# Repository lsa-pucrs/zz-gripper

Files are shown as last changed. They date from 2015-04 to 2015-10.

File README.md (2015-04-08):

# ZZ-Gripper v1.0

####Introdução: ####
Feita no laboratório de sistemas autônomos, [LSA](https://www.inf.pucrs.br/felipe.meneguzzi/lsa/), da FACIN na PUCRS.
Esta gripper foi desenvolvida no laboratório visando aplicações _pick-and-place_ em conjunto com o robo Turtlebot.

<p align="center">
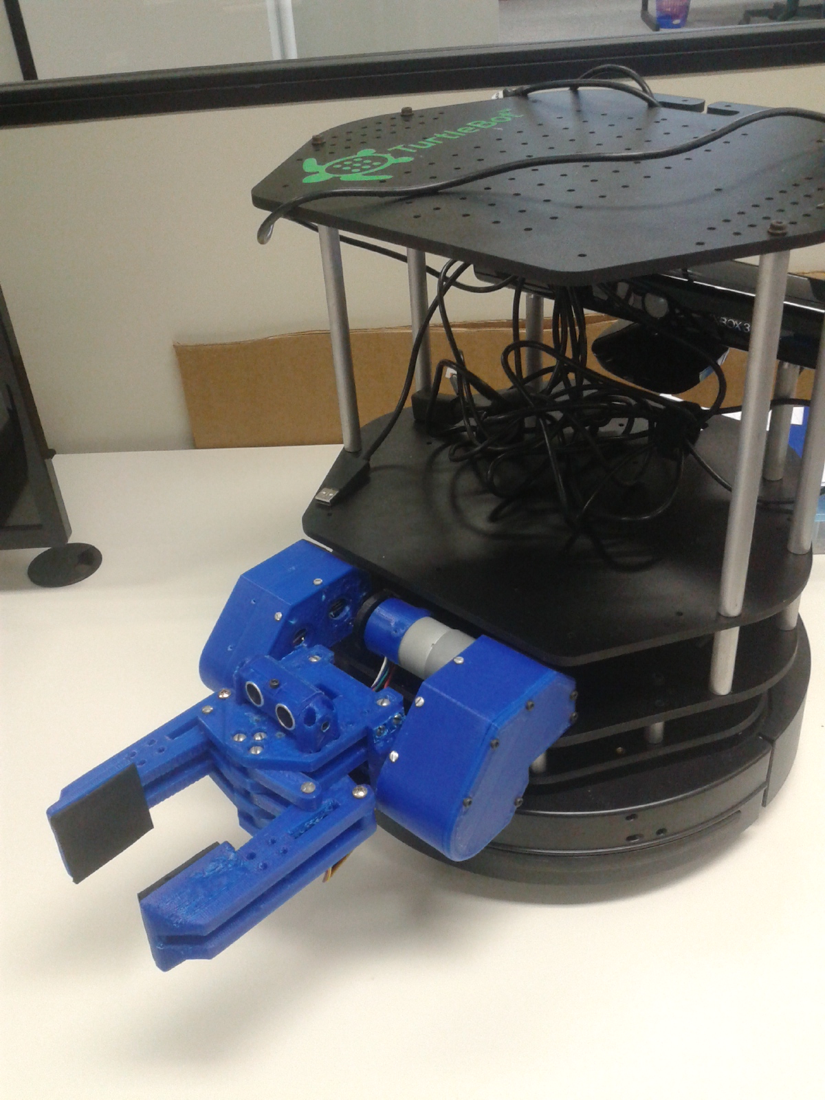
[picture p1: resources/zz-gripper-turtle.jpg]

</P>

####Especificações:####
+ Microcontrolador: Arduino nano
+ Driver: TB6612-Dual Motor Driver
+ Atuadores: 2 Graus de liberdade
+ Sensores: Sensor de força, sensor ultrasonico, sensor de corrente, chave fim de curso.
+ Peso (partes plasticas): ?
+ Peso total: ?
+ Custo total: ?
+ Tempo para construção: ?
+ Dimenções: ?
+ Força aplicada a objeto: ~500g
+ Peso máximo de sustentação: ~700g

####TO-DO_List:####
- [ ] Manual ZZ-Gripper v1.0
- [ ] Teste funcional por ssh (sem alimentação externa)
- [x] Projeto Solidworks
- [x] Driver exemplo ROS
- [x] Esquema elétrico da placa de controle

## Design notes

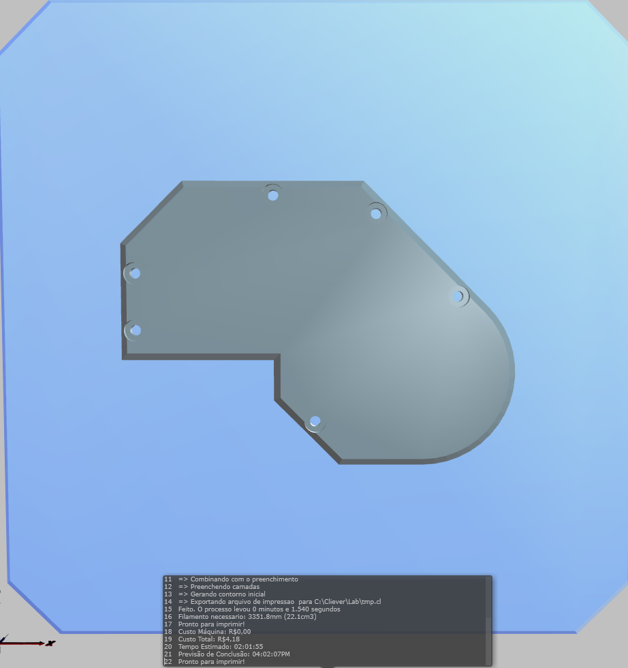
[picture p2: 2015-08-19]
stl_files/zz_gripper-specifications/gripper_support/motorPlate-board_lid.png

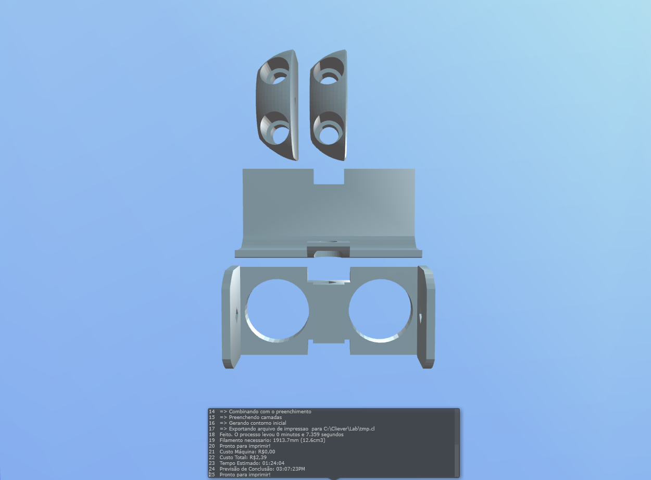
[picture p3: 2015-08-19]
stl_files/zz_gripper-specifications/sonar_support/sonar_support.png

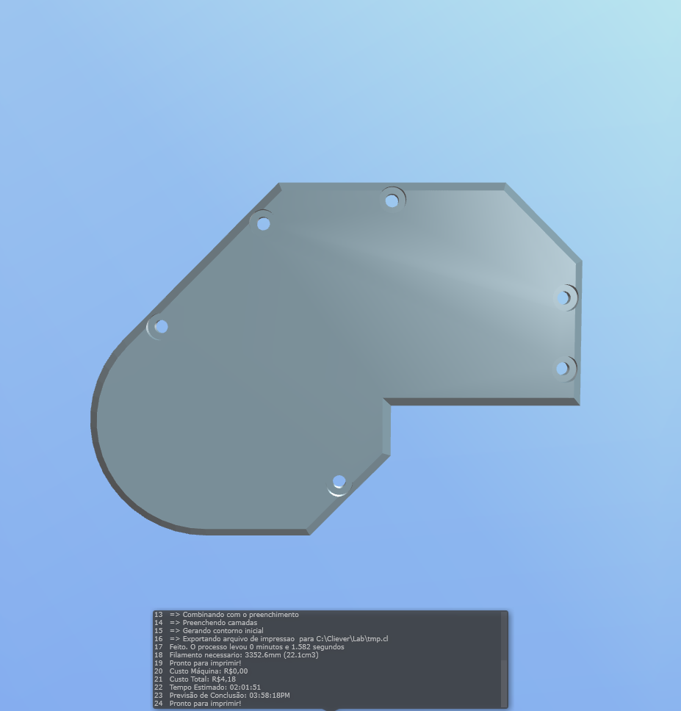
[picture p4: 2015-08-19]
stl_files/zz_gripper-specifications/gripper_support/motorPlate-lid.png

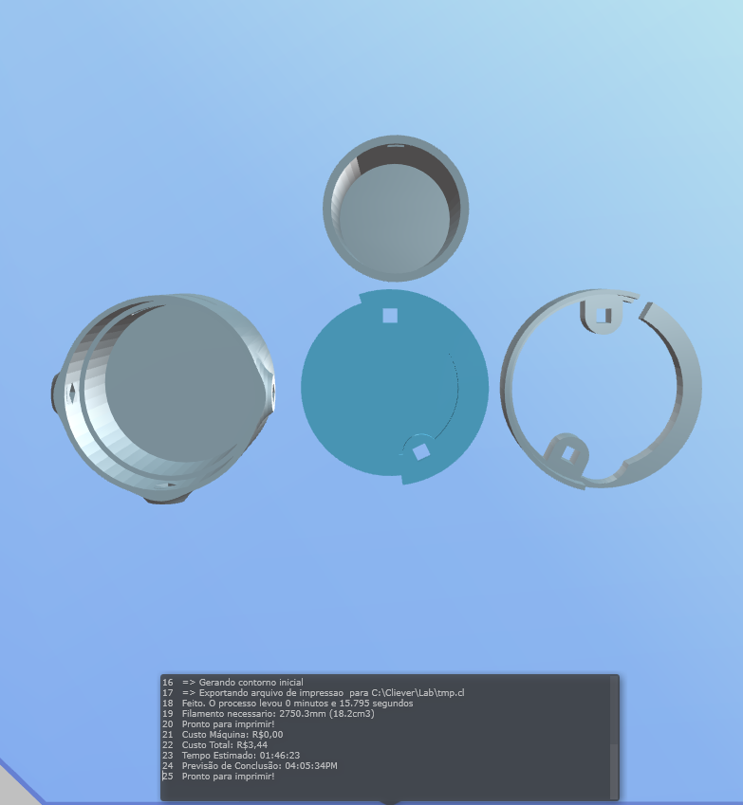
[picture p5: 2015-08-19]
stl_files/zz_gripper-specifications/gripper_support/motor_Case-and-board_protection.png

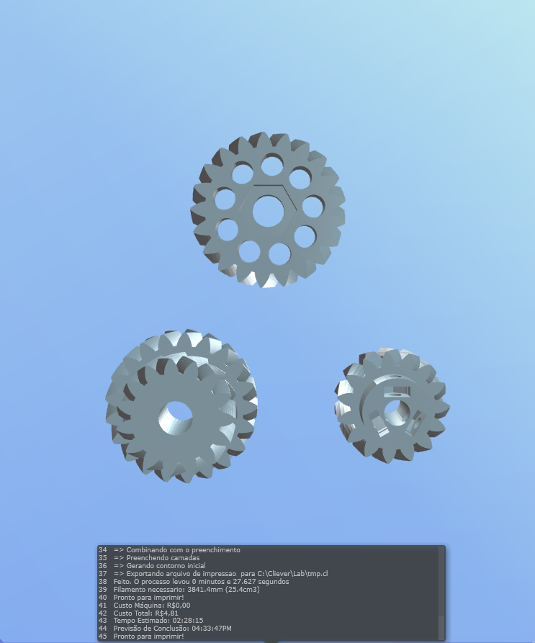
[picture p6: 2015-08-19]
stl_files/zz_gripper-specifications/gripper_support/gears/gears.png

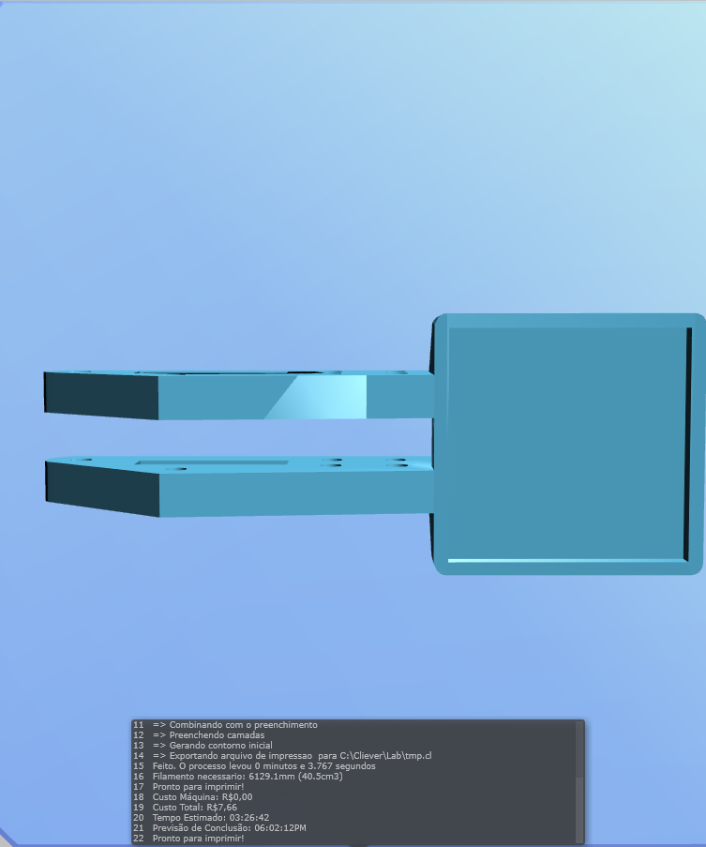
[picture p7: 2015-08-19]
stl_files/zz_gripper-specifications/gripper_hand/gripper_finger--DroidGripper-RightArm.png

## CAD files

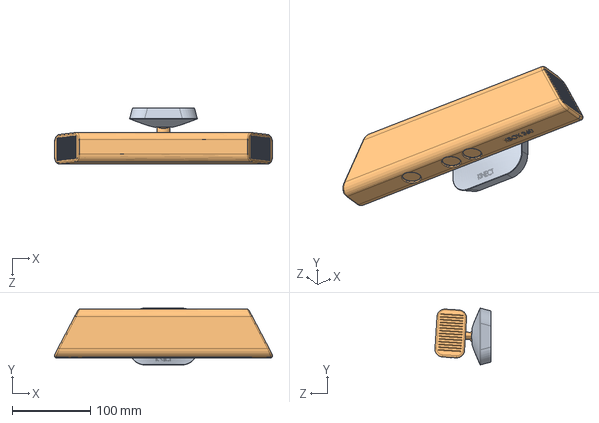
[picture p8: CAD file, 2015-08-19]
solidworks/turtlebot_2-converted_model/others/kinect/1_kinect_assembly.SLDASM
279.4 x 72.8 x 71.8 mm
base KINECT
KINECT XBOX

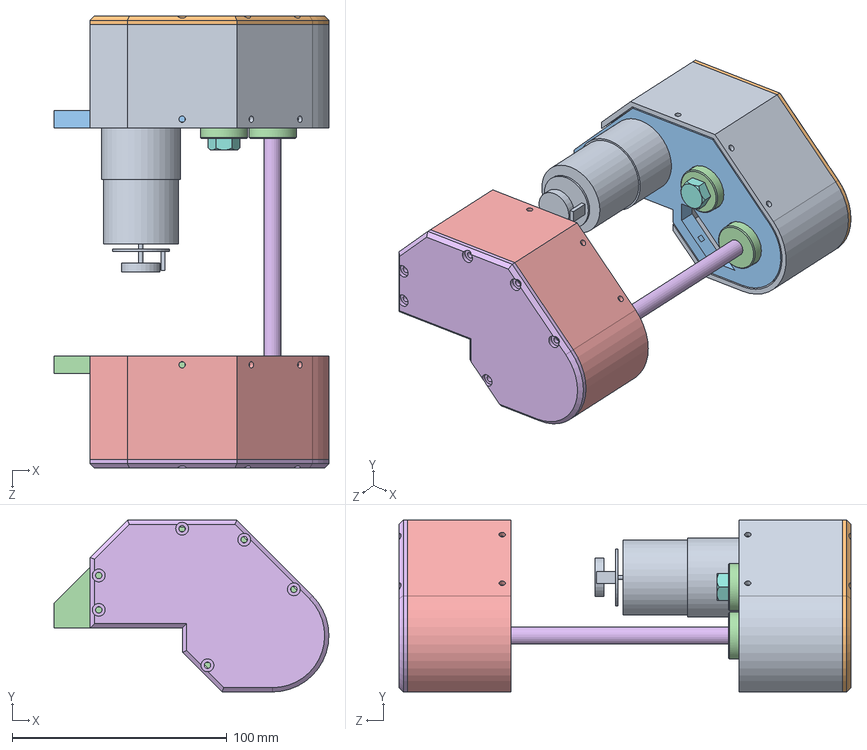
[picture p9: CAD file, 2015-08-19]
solidworks/zz_gripper-model/1_gripper_assembly.SLDASM
127.9 x 79.9 x 210.3 mm
motorPlate-case
motorPlate-lid
motorPlate
bearing x 4
nut x 3
threaded_rod
rod_gear_big_simple
bolt
motor_pololu
motor_gear_simple
reduction_gear_simple
motorPlate-board
motorPlate-board_case
motorPlate-board_lid

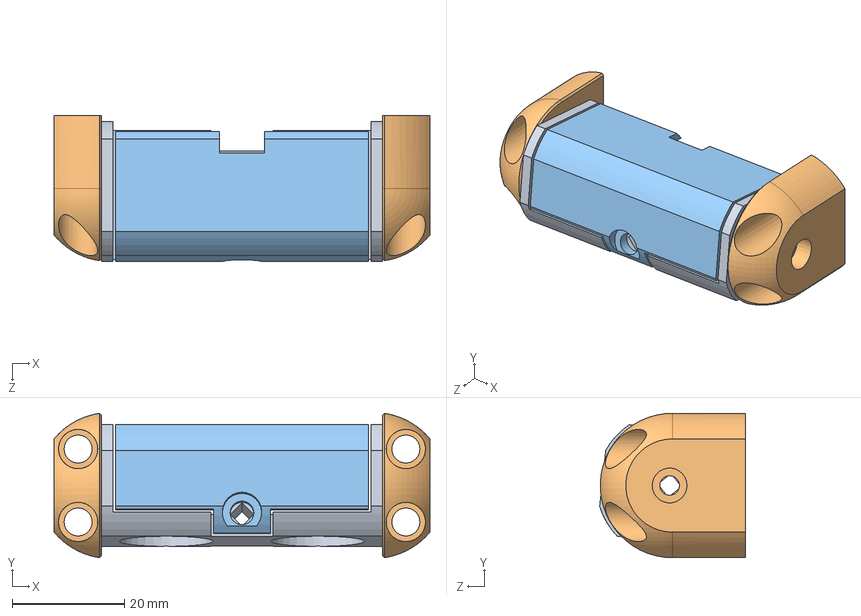
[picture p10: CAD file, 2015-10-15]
solidworks/zz_gripper-model/sonar_support/1_sonar_support_assembly.SLDASM
67.0 x 25.7 x 26.0 mm
sonar-case
sonar-support x 2
sonar-lid

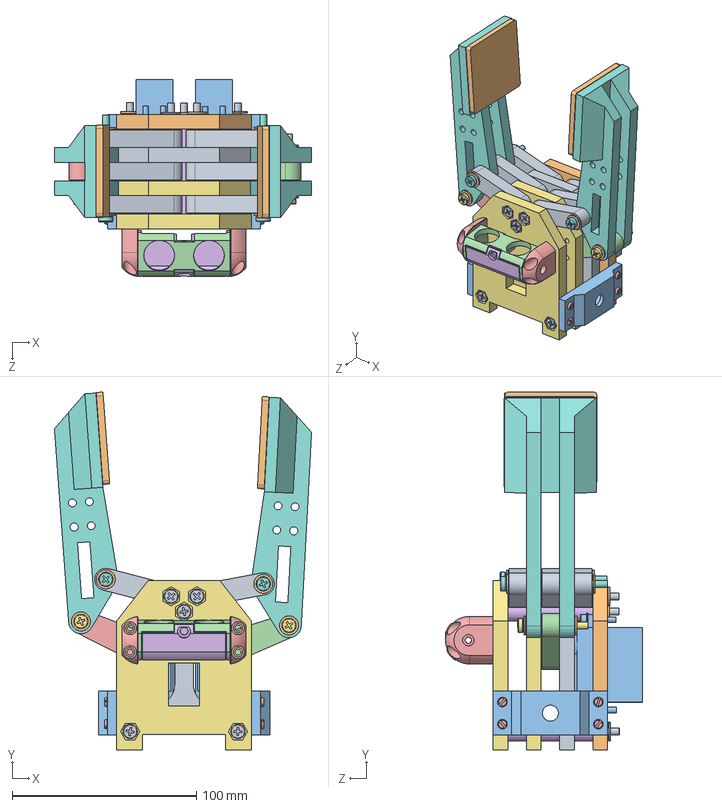
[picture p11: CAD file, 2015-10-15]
solidworks/zz_gripper-model/gripper_hand/1_hand_assembly.SLDASM
139.4 x 194.1 x 107.0 mm
gripperGearPlate
gripperServoPlate
MG996R_Another x 2
leftDriveGear
rightDriveGear
plate_spacer x 9
gripperSuportPlate x 2
gripper_finger x 2
gripper_interface_link x 6
pressurePlate x 2
main_axis_nut_reinforcement x 2
sonar-case
sonar-support x 2
sonar-lid
PPh-M4x35mm x 2
PPh-M4x55mm x 2
PPh-M4x65mm x 5
washer-M4 x 13
PA-M3x16mm x 8
washer-M3 x 8
FCA-2_85Dx13mm x 8

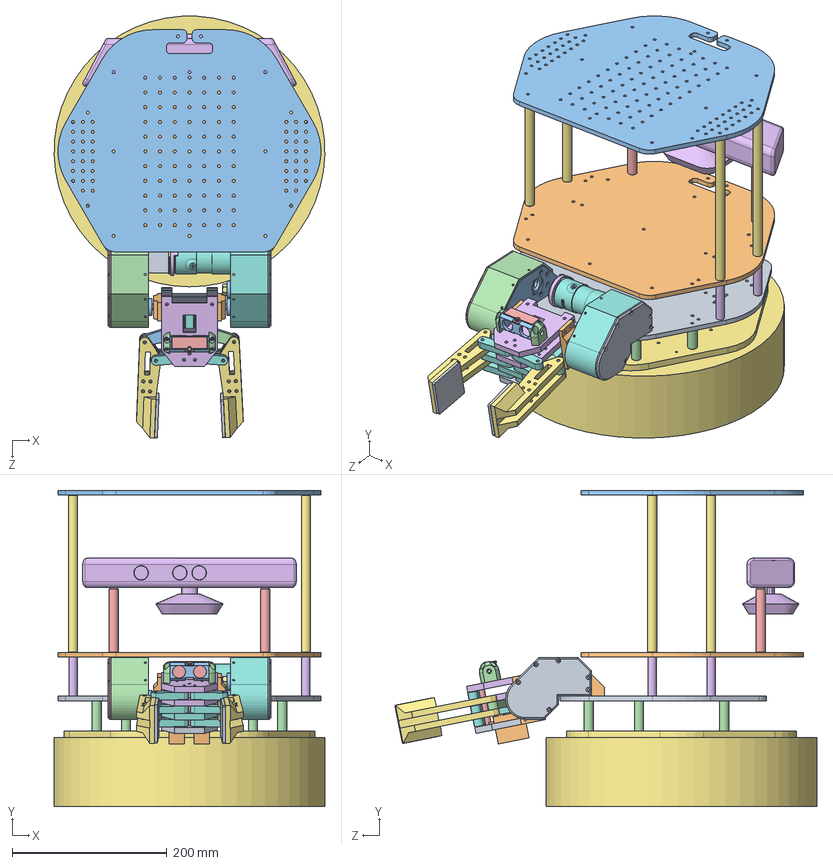
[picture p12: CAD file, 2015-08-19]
solidworks/turtlebot_2-converted_model/1_turtlebot_assembly.SLDASM
349.8 x 408.7 x 545.4 mm
plate_bottom
plate_middle_
plate_top_
pole_bottom_ x 6
pole_kinect_ x 2
pole_middle_ x 4
pole_top_ x 4
motorPlate-case
motorPlate-lid
motorPlate
bearing x 6
nut x 3
threaded_rod
rod_gear_big_simple
bolt
motor_pololu
motor_gear_simple
reduction_gear_simple
motorPlate-board
motorPlate-board_case
motorPlate-board_lid
Kinect_Sensor_68-04546
base
gripperGearPlate
gripperServoPlate
MG996R_Another x 2
leftDriveGear
rightDriveGear
plate_spacer x 9
gripperSuportPlate x 2
gripper_finger x 2
gripper_interface_link x 6
pressurePlate x 2
main_axis_nut_reinforcement x 2
sonar-case
sonar-support x 2
sonar-lid
motor_case-endstop_support
motor_case-endstop_support-lid
motor_case

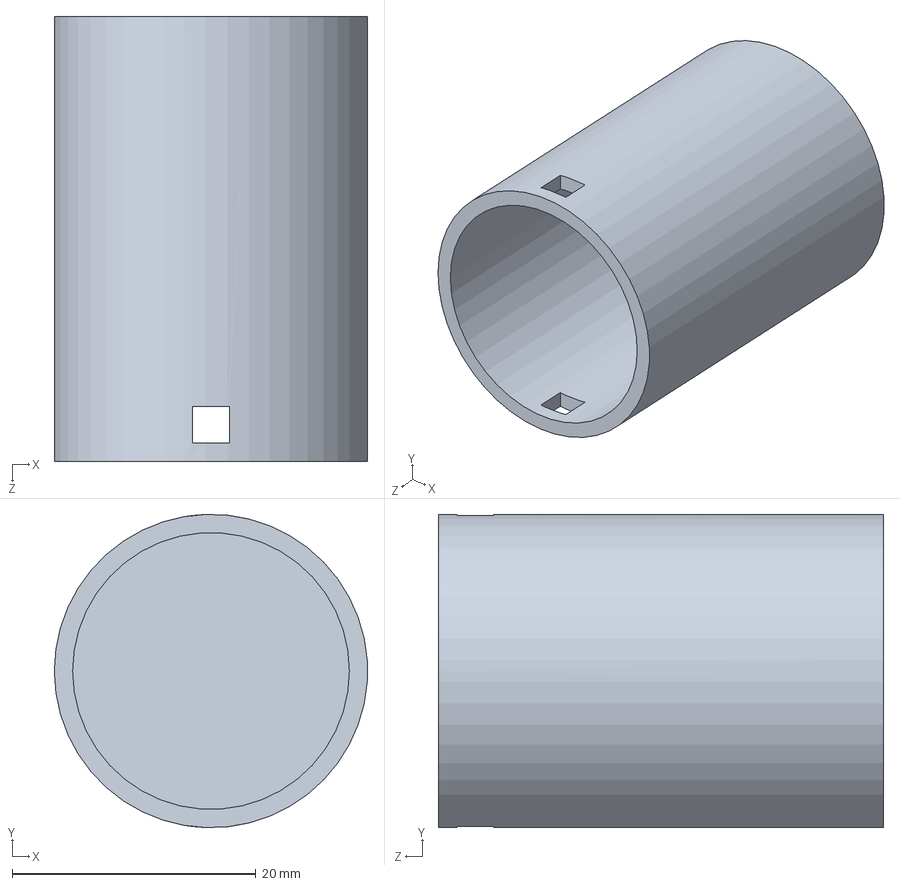
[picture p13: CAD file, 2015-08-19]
solidworks/zz_gripper-model/gripper_support/main_axys-board_protection.SLDPRT
25.7 x 25.7 x 36.5 mm

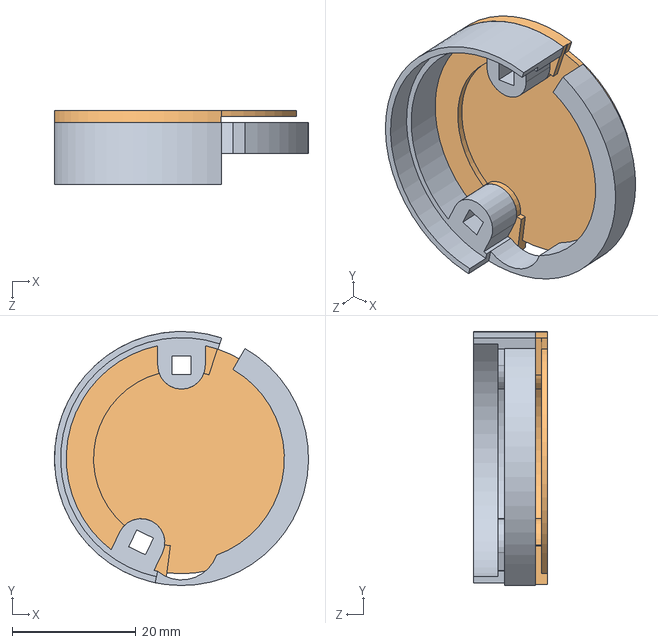
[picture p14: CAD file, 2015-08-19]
solidworks/zz_gripper-model/gripper_support/2_support_endstop.SLDASM
41.0 x 41.0 x 12.0 mm
motor_case-endstop_support
motor_case-endstop_support-lid

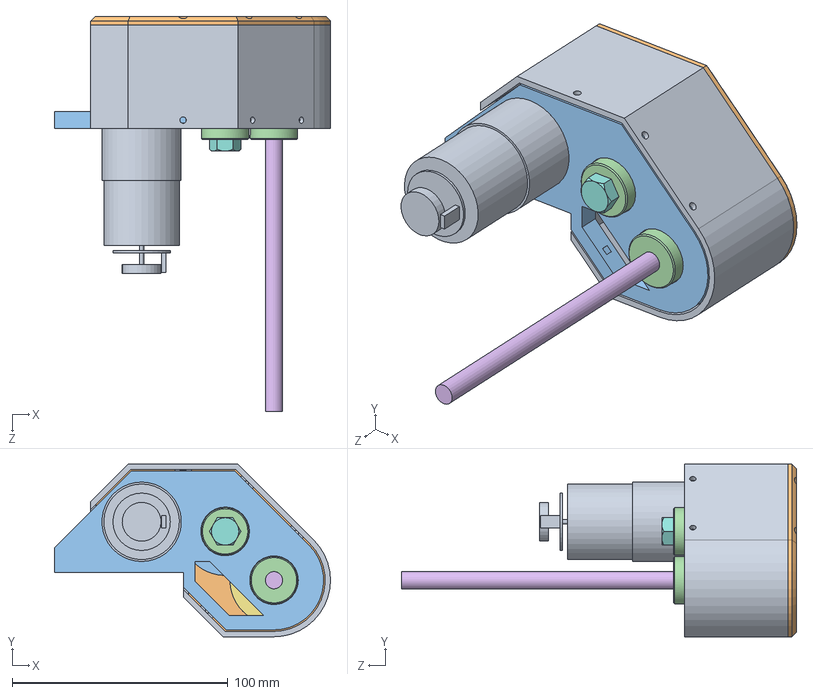
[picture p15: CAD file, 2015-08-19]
solidworks/zz_gripper-model/gripper_support/1_support_assembly.SLDASM
127.9 x 79.9 x 183.0 mm
motorPlate-case
motorPlate-lid
motorPlate
bearing x 4
nut x 3
threaded_rod
rod_gear_big_simple
bolt
motor_pololu
motor_gear_simple
reduction_gear_simple

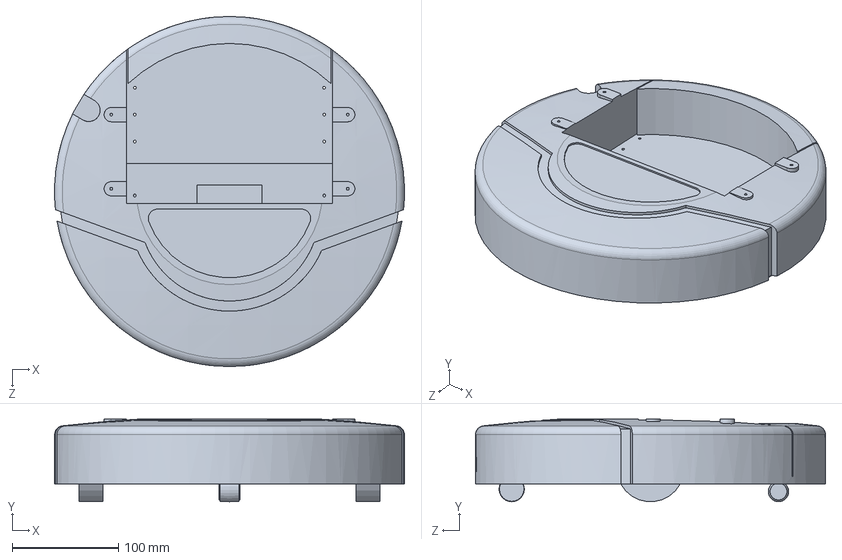
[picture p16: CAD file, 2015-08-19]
solidworks/turtlebot_2-converted_model/others/iRobot_Create_68-04545.SLDPRT
329.9 x 77.8 x 330.0 mm

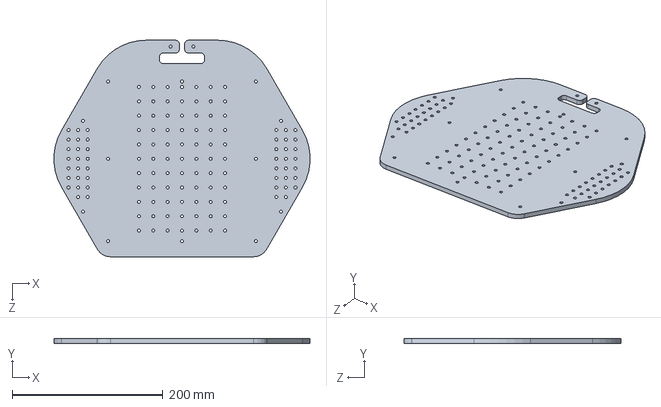
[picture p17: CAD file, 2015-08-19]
solidworks/turtlebot_2-converted_model/plate_top_.SLDPRT
339.6 x 6.00 x 287.3 mm

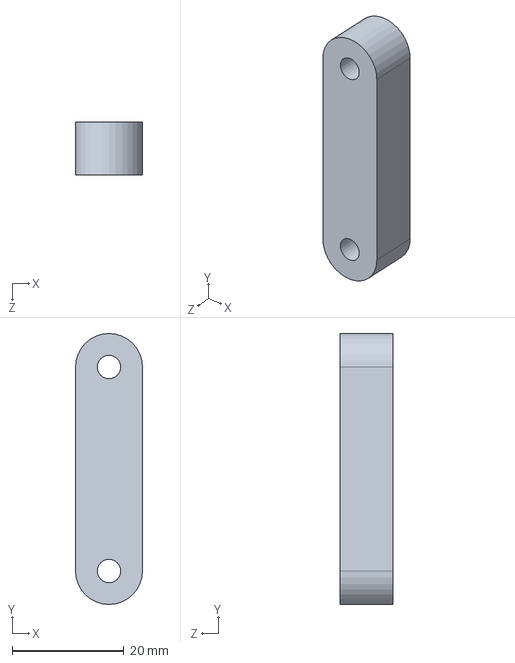
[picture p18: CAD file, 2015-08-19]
solidworks/zz_gripper-model/gripper_hand/converted/gripper_interface_link.SLDPRT
12.0 x 48.6 x 9.50 mm

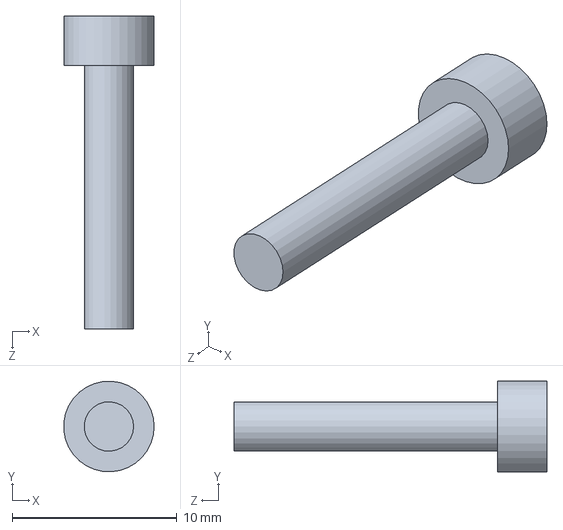
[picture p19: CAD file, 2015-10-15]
solidworks/zz_gripper-model/gripper_hand/resources/PA-M3x16mm.SLDPRT
5.49 x 5.49 x 19.0 mm

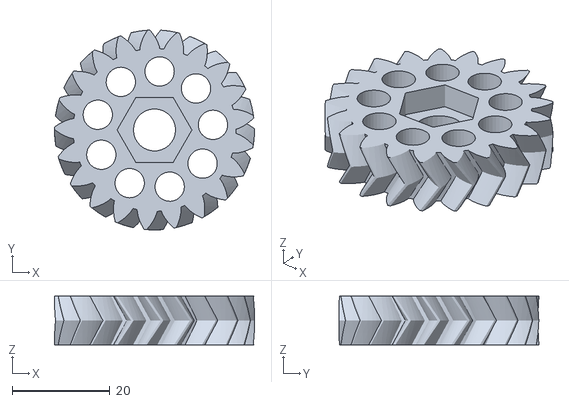
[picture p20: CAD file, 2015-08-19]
solidworks/zz_gripper-model/gripper_support/gears/rod_gear_big.stl
40.9 x 40.9 x 10.0

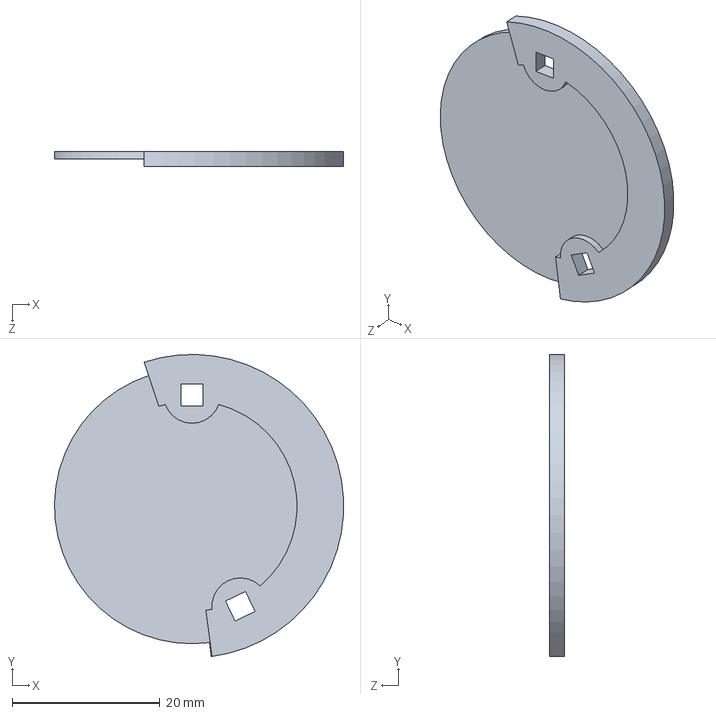
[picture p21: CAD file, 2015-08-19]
solidworks/zz_gripper-model/gripper_support/motor_case-endstop_support-lid.SLDPRT
39.1 x 40.8 x 2.00 mm

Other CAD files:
solidworks/zz_gripper-model/gripper_support/others/motor_pololu.SLDPRT
stl_files/zz_gripper-parts/gripper_hand/6x-gripper_interface_link--DroidGripper-InterfaceLinks.stl
stl_files/zz_gripper-parts/gripper_hand/new_parts/6x-plate_spacer.STL
stl_files/zz_gripper-parts/sonar_support/2x-sonar-support.STL
solidworks/zz_gripper-model/gripper_support/gears/motor_gear.scad
solidworks/zz_gripper-model/gripper_support/gears/reduction_gear.scad
solidworks/zz_gripper-model/gripper_support/gears/rod_gear_big.scad
solidworks/zz_gripper-model/gripper_support/gears/resource/rod_gear.scad
solidworks/turtlebot_2-converted_model/base.SLDPRT
solidworks/turtlebot_2-converted_model/counterweight_.SLDPRT
solidworks/turtlebot_2-converted_model/others/Kinect_Sensor_68-04546.SLDPRT
solidworks/turtlebot_2-converted_model/others/kinect/KINECT XBOX.SLDPRT
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

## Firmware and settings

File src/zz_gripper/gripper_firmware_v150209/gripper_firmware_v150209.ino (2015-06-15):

/*
Force Sensor A201-25 (0-25 lb. force range 111.205N) acessado em http://www.phidgets.com/documentation/Phidgets/3100_0_FlexiforceUserManual.pdf
Rotation Speed ~38.27rpm source: Motor Pololu 70:1 = 150RPM em 12v =  (((15.0/21)**2)*150)/2^= ~38.27

Servo mg996:
Velocidade de operação: 0.13sec / 60 graus (6.0V sem carga) = 0.174seg 80graus
Torque Stall: 15 kg-cm (208,3 oz-in) em 6V
*/
#include "gripper_firmware.h"
#include <PWMServo.h> //tem que estar no .h e no sketch
#include <ros.h>
#include <std_msgs/String.h>
#include <std_msgs/UInt8.h>
#include <std_msgs/UInt16.h>
#include <std_msgs/Int16.h>



ros::NodeHandle nh;

void callCommand( const std_msgs::String& gripper_msg){
  readString=gripper_msg.data;
}

std_msgs::String status_msg;
std_msgs::UInt16 topicSpeed;
std_msgs::Int16 topicPosition;
std_msgs::UInt8 topicDistance;
std_msgs::UInt16 topicForce;
std_msgs::Int16 topicRotationX;

ros::Subscriber<std_msgs::String> subGripperCommands("gripperCommands" , callCommand);

ros::Publisher advGripperSpeed("gripperSpeed", &topicSpeed);
ros::Publisher advGripperForce("gripperForce", &topicForce);
ros::Publisher advGripperPosition("gripperPosition", &topicPosition);
ros::Publisher advGripperDistance("gripperDistance", &topicDistance);
ros::Publisher advGripperRotationX("gripperRotationX", &topicRotationX);

void setup()   {
  pinMode(dirPin,OUTPUT);
  pinMode(pwmPin,OUTPUT);
  pinMode(inputBPin,INPUT); //inputB // white wire
  pinMode(homePin,INPUT);
  attachInterrupt(inputAPin,incA,FALLING); //pin 2 inputA // yellow wire

  //gripper
  gpp_R.attach(servoRPin);  
  gpp_L.attach(servoLPin);
  //#gripper
  nh.initNode();
  nh.subscribe(subGripperCommands);
  nh.advertise(advGripperSpeed);
  nh.advertise(advGripperForce);
  nh.advertise(advGripperPosition);
  nh.advertise(advGripperDistance);
  nh.advertise(advGripperRotationX);

  nh.spinOnce();
  delay(50);
}



void loop(){
  //ROS PUBLISHERS
  topicForce.data = gripperForce;
  advGripperForce.publish(&topicForce);
  topicPosition.data = gripperPosition;
  advGripperPosition.publish(&topicPosition);
  topicRotationX.data = gripperRotationX;
  advGripperRotationX.publish(&topicRotationX);
  topicDistance.data = gripperDistance;
  advGripperDistance.publish(&topicDistance);

  //encoder dalay
  time = millis();
  unsigned long rotationDelay = time - lastTimeRotationDelay;
  if(rotationDelay >= gripperSpeedSetPoint/10){ // dividido por 10 pois, 5ms é o delay ideal dealy deafault: 50ms
    lastTimeRotationDelay = time;
    if(ComposedSetPoint<gripperRotationXSetPoint)ComposedSetPoint++;
    if(ComposedSetPoint>gripperRotationXSetPoint)ComposedSetPoint--;
    computeEncoderX(ComposedSetPoint);
  }


  //compute command delay
  time = millis();
  unsigned long wait = time - lastTime;  
  if(wait >= 100){ //amory: declarar como constante
    lastTime = time;
    computeCommand(readString);
    //gripperForce = analogRead(forceSensorPin);//map(gripperForce,0,111,1023,0); //4.2v = 111N = 11.34kg
    //gripperDistance = measureDistance();
    //gripperCurrent = analogRead(currentSensorPin);
  }

  updateGripperActions();

  unsigned long waitSpinOnce = time - lastTimeSpinOnce;  
  if(waitSpinOnce >= 50){ 
    lastTimeSpinOnce = time;
    nh.spinOnce(); //evitar delay pois afeta na movimentacao da gripper
  }
}

void incA(){
  inputB = digitalRead(inputBPin);
  if(inputB)gripperRotationX--;
  else gripperRotationX++;
}

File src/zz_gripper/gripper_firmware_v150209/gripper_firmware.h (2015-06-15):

#include "Arduino.h" //needed for Serial.println
#include <PWMServo.h> 

//digital pins
#define servoRPin 10
#define servoLPin 9
#define trigPin 8 
#define echoPin 7 
#define pwmPin 6
#define dirPin 5
#define inputBPin 4
#define homePin 3
#define inputAPin 0 //interrupt 0 -> pin 2

//analogic pins
#define forceSensorPin 0
#define BAUDRATE 9600


//commandVariables
String readString; //para entrada serial
String commandName="";
int16_t commandValue=0;
boolean commandDone = false;

//gripperVariables
boolean gripperActive = true;
uint16_t gripperSpeedSetPoint = 50;
int16_t gripperPosition;
int16_t gripperPositionSetPoint;
int8_t gripperMode = 0; //0 open/ 1 close/ 2 auto
int8_t lastGripperMode = 1;
PWMServo gpp_R;  
PWMServo gpp_L; 
boolean gripperState = false;
//Right 45 min, 60 mid, 150 max 
int16_t gpp_RMax = 136;///160;
int16_t gpp_RMin = 55;
//Left 145 min, 120 mid, 50 max
int16_t gpp_LMax = 34; //30
int16_t gpp_LMin = 120;
//////////////////////////
int16_t gpp_RPos = gpp_RMin;
int16_t gpp_LPos = gpp_LMin;

//sonar
uint8_t gripperDistance;
uint8_t gripperDistanceSetPoint = 15;
boolean sonarActive = false;
boolean sonarFlag = false; //when it found something

//forceSensor
uint16_t gripperForce;
uint16_t gripperForceSetPoint = 50; //hard 0; easy 1024; to activate

//encoder
int16_t ITerm1 = 0, ITerm2 = 0;
int16_t ComposedSetPoint;
int16_t gripperRotationXSetPoint;
volatile int16_t gripperRotationX = 0;
volatile boolean inputB = false;
double n = 0;
double pwmValue = 0;

//general
int val;
unsigned long time;
unsigned long lastTime;
unsigned long lastTimeCloseDelay;
unsigned long lastTimeRotationDelay;
unsigned long lastTimeSpinOnce;

///////////////////////////////////////////////////////////////////////////////
//FUNCTIONS DECLARATIONS 
///////////////////////////////////////////////////////////////////////////////
void computeCommand(String rawInput);
void updateGripperActions();
void helpToPrint();
boolean close();
boolean close(int newPos);
boolean close(uint16_t newPos,uint16_t newSpeed);
boolean open();
boolean closeRoutine();
void computeEncoderX(int16_t setPoint);
void homeRoutine();
uint8_t measureDistance();

///////////////////////////////////////////////////////////////////////////////
//MAIN FUNCTION
///////////////////////////////////////////////////////////////////////////////
void computeCommand(String rawInput){
  String auxName = "";
  int16_t auxValue = 0;
  int firstCharIndex = rawInput.indexOf('_');
  if(firstCharIndex<0) firstCharIndex = rawInput.indexOf(' '); //multiplos comandos
  if(firstCharIndex>0){
    String numberCommand = "";
    for(int i = firstCharIndex+1; i < rawInput.length(); i++){ //se rawInput.length()-1 nao le a ultima string
      numberCommand += rawInput[i];
    }
    auxValue = numberCommand.toInt();
    for(int i = 0; i < firstCharIndex; i++){
      auxName+=rawInput[i];
    }
  }
  else{ //if index <= 0
    auxValue = rawInput.toInt();
    auxName = rawInput; 
  }
  if(commandValue!=auxValue||commandName!=auxName){
    commandDone=false;
    commandValue=auxValue;
    commandName=auxName;
  }
}

void updateGripperActions(){
  if(commandName=="help")helpToPrint();
  else if(commandName=="close"){
    if(commandValue==101){
      if(sonarFlag)sonarActive = false;
      else sonarActive = true;
      close();
    }
    else close(commandValue);
  }
  else if(commandName=="open"){
    sonarFlag = false; //para resetar sonar na closeRoutine()
    open();
  }
  else if(commandName=="setForce")gripperForceSetPoint = commandValue;
  else if(commandName=="setSpeed")gripperSpeedSetPoint = commandValue;
  else if(commandName=="setDistance")gripperDistanceSetPoint = commandValue;
  else if(commandName=="rotate")gripperRotationXSetPoint = commandValue;
  else if(commandName=="home")homeRoutine();
  //else rosPrint("Unknown command!");
}


/*void rosPrint(char message){
  std_msgs::String msg;
  msg.data = message;
  nh.loginfo(msg.data);
  //nh.loginfo("msg");
}*/

void helpToPrint(){}

boolean close(){return close(100);}
boolean close(int newPos){return close(newPos,gripperSpeedSetPoint);}
boolean close(uint16_t newPos,uint16_t newSpeed){
  if(closeRoutine()){
    int16_t setPointR = map(newPos,0,100,gpp_RMin,gpp_RMax);
    int16_t setPointL = map(newPos,0,100,gpp_LMin,gpp_LMax);
    time = millis();
    unsigned long closeDelay = time - lastTimeCloseDelay;
    if(closeDelay >= newSpeed){ 
      lastTimeCloseDelay = time;
      if(gpp_RPos<setPointR)gpp_RPos+=1; //close R
      if(gpp_RPos>setPointR)gpp_RPos-=1; //open R
      if(gpp_LPos>setPointL)gpp_LPos-=1; //close L
      if(gpp_LPos<setPointL)gpp_LPos+=1; //open L 
      gpp_R.write(gpp_RPos);
      gpp_L.write(gpp_LPos); 
      return true;
    }
    
  }
  return false;
}

boolean open(){
  gpp_RPos = gpp_RMin;
  gpp_LPos = gpp_LMin;
  gpp_R.write(gpp_RPos); //45 min, 60 mid, 150 max  
  gpp_L.write(gpp_LPos);//145 min, 120 mid, 50 max
}

boolean closeRoutine(){
  gripperForce = analogRead(forceSensorPin);//map(gripperForce,0,111,1023,0); //4.2v = 111N = 11.34kg
  if(gripperForce>gripperForceSetPoint)return false; 

  if(sonarActive){
    gripperDistance = measureDistance();
    if(gripperDistance>gripperDistanceSetPoint)return false;
    else sonarFlag = true;
  }
  return true;
}

void computeEncoderX(int16_t setPoint){
  int16_t input = gripperRotationX; 
  int16_t erro = input - (-1*setPoint); // -1* inverte rotacao
  int16_t erro1 = map(erro,0,600,0,-255); //255 é o valor maximo do pwm
  int16_t erro2 = map(erro,0,600,0,255); // 600 pulsos, é o angulo max (90°)
  float kp=10;
  int16_t output1 = kp*erro1;
  int16_t output2 = kp*erro2;
  if(output1>255)output1=255;
  else if(output2>255)output2=255;
  if(output1<0)output1=0; //120 -> pwm minimo para mover a garra
  else if(output2<0)output2=0;

  analogWrite(dirPin,output1);
  analogWrite(pwmPin,output2); //0   
}

void homeRoutine(){
  open();
  gripperRotationX = 0;
  uint16_t homePos = 0;
  while(!digitalRead(homePin)){
    homePos--;
    computeEncoderX(homePos);
    delay(5);
  }
  gripperRotationX = 0;
  gripperRotationXSetPoint=450;
}

/*
void homeRoutine(){
  open();
  uint16_t homePos = 0;
  while(!digitalRead(homePin)){
    homePos--;
    computeEncoderX(homePos);
    delay(5);
  }
  homePos = 0;
  gripperRotationX = 0;
  gripperRotationXSetPoint=450;

  while(homePos<450){
    homePos++;
    computeEncoderX(homePos);
    delay(5);
  }
}*/
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

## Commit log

2015-08-19 Modelo 3D corretamente posicionado na turtlebot
    [1_gripper_assembly.SLDASM, 1_hand_assembly.SLDASM, 1_kinect_assembly.SLDASM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]
2015-10-15 Imagens das partes impressas para colocar na documentação
2015-10-15 parafusos principais adicionados
    [1_hand_assembly.SLDASM, 1_sonar_support_assembly.SLDASM, PA-M3x16mm.SLDPRT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]
